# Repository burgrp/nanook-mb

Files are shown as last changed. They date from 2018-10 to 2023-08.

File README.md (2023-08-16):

# NANOOK main control board

Nanook-mb is control board for open source [NANOOK ground-water heat pump](https://cad.onshape.com/documents/2a5990c1c14b1713fdde9141/w/393a2c463278bded31251c68/e/64a137d08251e156e9e96024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) project. The board is responsible for:

- soft-switching three phases compressor
- switching two circulation pumps
- controlling Carel Electronic Expansion Valve
- reading
  - safety low and high pressure switches
  - water temperature sensors on all exchanger ports (eight sensors in total)
  - water pressure sensors on cold and hot side
  - water flow sensors on cold and hot side
  - refrigerant pressure sensors on cold and hot side
- providing configuration web user interface via WiFi connection

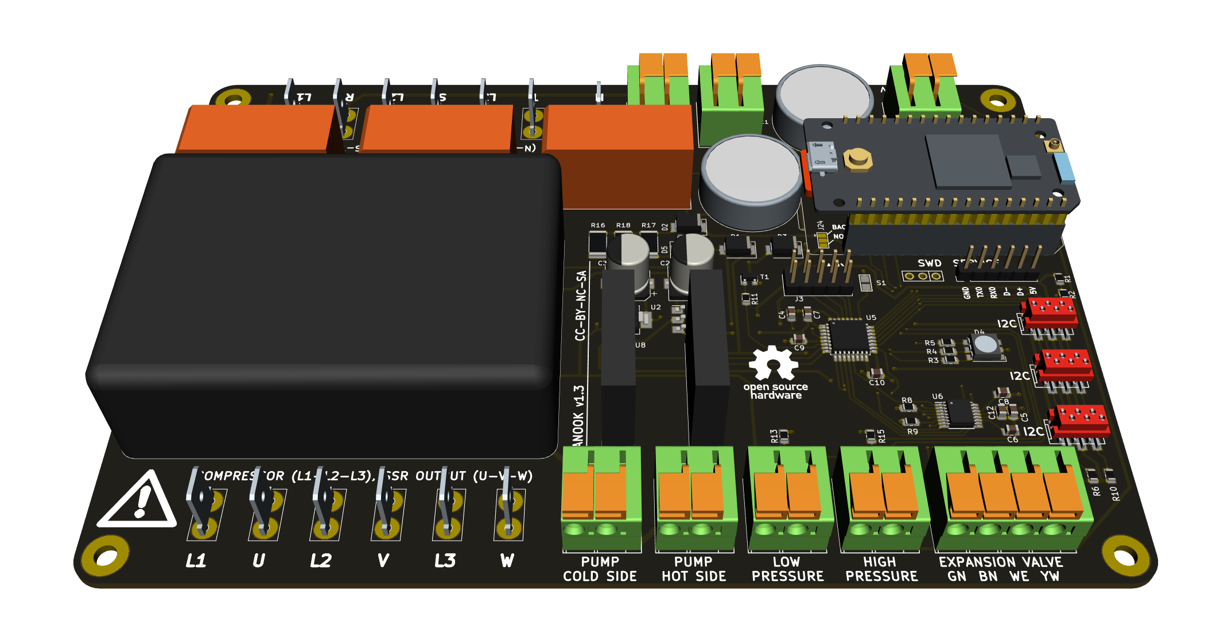
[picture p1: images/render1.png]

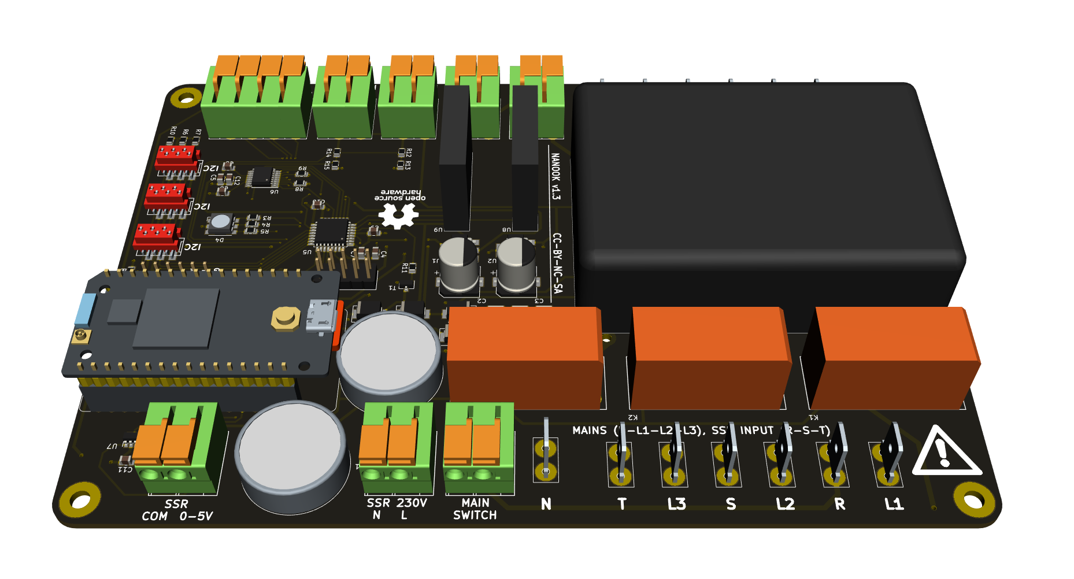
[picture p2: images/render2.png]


## Safety warnings
TBD: grounding, connectors, switching (rocker vs. ext. CB)

## System connections

### Diagram
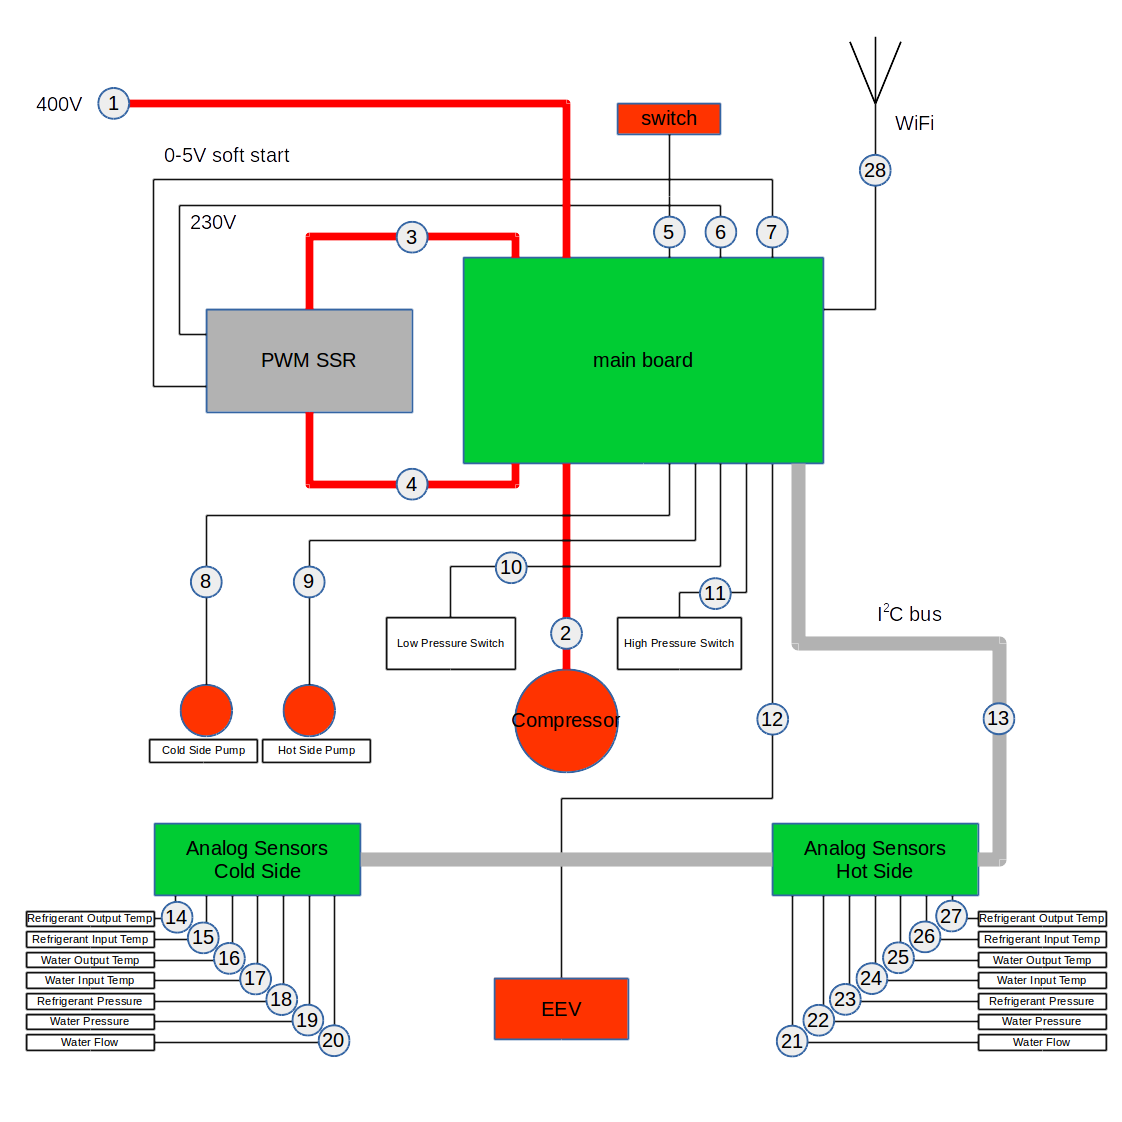
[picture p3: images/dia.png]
Block Diagram


### Wiring

#### Mains to MB (#1)
Connection to mains is done by flexible cable 5x 2.5mm<sup>2</sup>. Mains side should be connected to on-wall box with dedicated circuit breaker (3x16A). Board side end must be terminated with insulated Faston 6.3 connectors and connected to L1, L2, L3 and N terminals of the board. To avoid contact with metal chassis, use angled Fastons only.

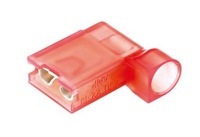
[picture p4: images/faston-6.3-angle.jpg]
Insulated Faston 6.3


Ground wire must be terminated by crimp eye-type connector and mounted by screw to chassis.

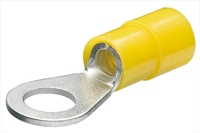
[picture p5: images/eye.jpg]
Eye-type connector


### MB to compressor (#2)
This is, with #1, another high-current connection done by 3x 2.5mm<sup>2</sup> cable. Both sides must be terminated by 6.3 Fastons.

### MB to PWM SSR power lines (#3, #4)
These are six 2.5mm<sup>2</sup> wires terminated by 6.3 Fastons on board side and by eye on SSR side. Make sure all six wires (R, S, T, U, V, W) are connected to properly.

### MB to ON/OFF switch (#5)
There is a rocker switch to turn heat pump ON and OFF. The switch just disconnects onboard power supply, which in turn opens onboard coil relays. This means that the board is still powered even with the rocker switch turned off.

### MB to PWM SSR control lines (#6, #7)
These lines connects main board and PWM SSR control circuit. Two lines supply the control circuit with 230V AC power (#6). The other two are control signal 0-5V. Leave SSR contacts 4-20mA and +5V unconnected.

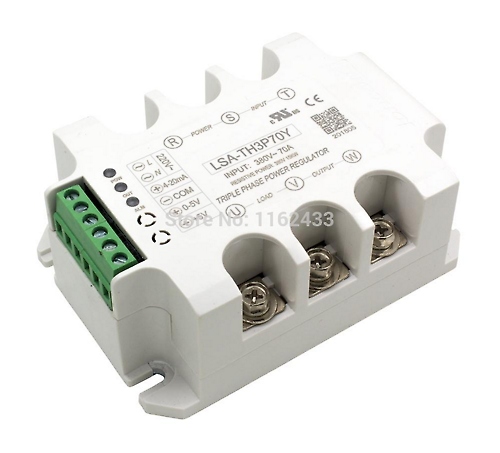
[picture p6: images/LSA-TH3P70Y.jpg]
LSA-TH3P70Y


### MB to circulation pumps (#8, #9)
The main board directly controls primary (cold) and secondary (hot) side circulation pumps. Onboard SSRs are rated to 100W max power output.

### MB to safety pressure switches (#10, #11)
Connections to safety pressure switches on low pressure and high pressure sides.

### MB to electronic expansion valve (#12)
For wires of EEV stepper motor. Color coding for Carel valves is marked on PCB:
- GN - green
- BN - brown
- WE - white
- YW - yellow.

### I<sup>2</sup>C bus (#13)
There are three connectors on board, all of them sharing single I<sup>2</sup>C bus. Analog sensor boards are connected by 6-wire flat cable with crimped Micro-Match connectors.

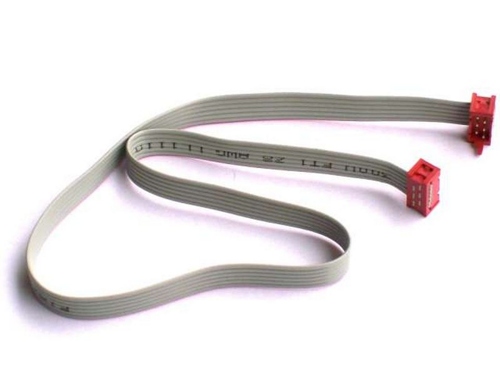
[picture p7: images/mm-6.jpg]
Micro-Match cable


There may be two separate cables for each analog sensors board, or there may be single cable shared by both analog sensors boards.

### Analog sensors board to temperature sensors (#14, #15, #16, #17, #24, #25, #26, #27)
Temperatures are measured by NTC 10K 1% 3950 thermistors.

There are waterproof thermistors with JST-XH connectors available. They may be used directly with no additional crimping needed.

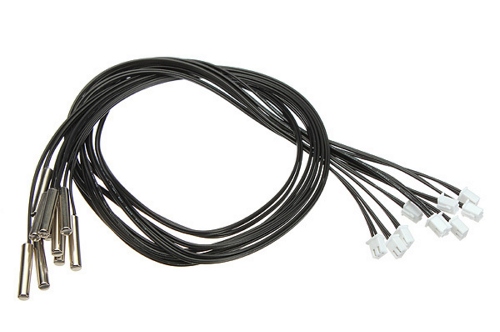
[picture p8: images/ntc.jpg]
Waterproof NTC with JST-XH


Thermistors should be tightly mounted on appropriate pipes, ideally with thermal conductive paste and outer environment insulation cover.

Thermistors are located as follows:
- #14: "cold side refrigerant output" - evaporator refrigerant output to compressor suction
- #15: "cold side refrigerant input" - EEV to evaporator refrigerant input
- #16: "cold side water output" - evaporator water output to collector input
- #17: "cold side water input" - collector output to evaporator water input
- #24: "hot side water input" - cold water from heating system to condenser water input
- #25: "hot side water output" - hot water from condenser to heating system
- #26: "hot side refrigerant input" - compressor discharge to condenser refrigerant input
- #27: "hot side refrigerant output" - condenser refrigerant output to EEV or refrigerant accumulator

### Analog sensors board to pressure sensors (#18, #19, #22, #23)
Pressure sensors are available either with other connectors than JST-XH or with no connector at all. You need to crimp proper three wire JST-XH connectors as:

- 1: GND (black)
- 2: SIGNAL (yellow)
- 3: +5V (red)

and for Carel sensors with green, white and black wires as:

- 1: GND (green)
- 2: SIGNAL (white)
- 3: +5V (black)

Pressure sensors are located as follows:
- #18: "cold side refrigerant pressure" - compressor suction, -1...9,3bar => 0...5V, recommended SPKT0013RO
- #19: "cold side water pressure" - collector water loop, 0...1.2MPa => 0...5V
- #22: "hot side water pressure" - heating system water loop, 0...1.2MPa => 0...5V
- #23: "hot side refrigerant pressure" - compressor discharge, 0...34,5bar => 0...5V, recommended SPKT0033RO

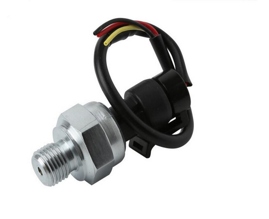
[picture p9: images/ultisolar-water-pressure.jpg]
Ultisolar water pressure sensor 0...1.2MPa


Ultisolar water pressure sensor 0...1.2MPa

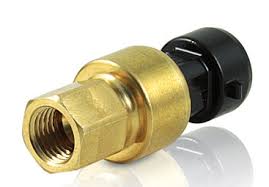
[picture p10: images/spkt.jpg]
Carel SPKT refrigerant pressure sensor


Carel SPKT refrigerant pressure sensor

### Analog sensors board to water flow sensors (#20, #21)
Water flow sensors are available either with other connectors than JST-XH or with no connector at all. You need to crimp proper three wire JST-XH connectors as
- 1: GND (black)
- 2: SIGNAL (yellow)
- 3: +5V (red)

Water sensors are located as follows:
- #20: "cold side water flow" - collector water loop
- #21: "hot side water flow" - heating system water loop

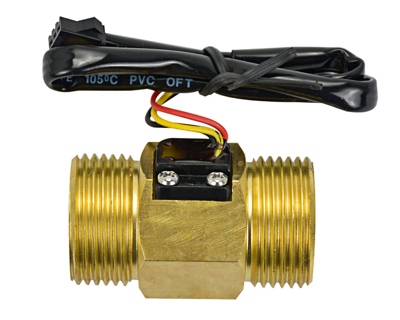
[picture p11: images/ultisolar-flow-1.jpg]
Ultisolar flow sensor


USC-HS10TA BSP is a suitable water flow sensor

### MB to WiFi antenna (#28)

Main board is connected to network by WiFi. Although there is small chip antenna integrated on board, an external antenna is needed because of metal enclosure. Connect a 2.4GHz antenna by IPEX connector.

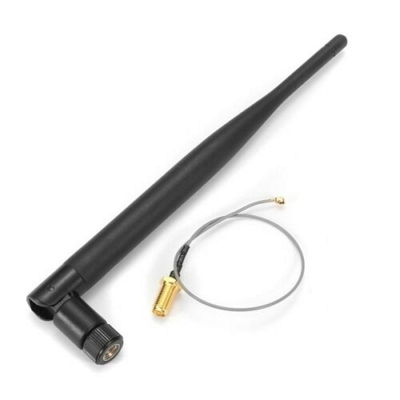
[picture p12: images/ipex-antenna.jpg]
IPEX 2.4GHz panel mount antenna


## Compiling firmware
In order to compile and flash firmware, you need to install Node.js, openocd and arm-none-eabi GCC.

Source code is written our [Silicon build system](https://github.com/device-farm/silicon).
Install Silicon by:
```sh
sudo npm install -g @device.farm/silicon
```

And then build and flash by:
```sh
silicon build -dsf
```

The `-f` parameter instructs Silicon to flash the image using openocd, which should be connected to your MCU and listening on port 4444.

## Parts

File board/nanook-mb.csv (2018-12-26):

Quantity | Designator | Designation
2 | C13,C1 | 2F
4 | REF**,REF**,REF**,REF** | MountingHole_3.7mm_Pad
3 | K3,K1,K2 | RELAY_2
6 | C4,C7,C9,C10,C11,C12 | 100n
1 | C5 | 10u
1 | C6 | 10n
1 | C8 | 2.2M
4 | D1,D3,D2,D5 | SK22
1 | J1 | Power Switch
1 | J3 | AUX
1 | J4 | E2V
1 | J5 | LPS
1 | J6 | Pump Cold Side
1 | J7 | Pump Hot Side
1 | J8 | HPS
9 | R1,R2,R6,R7,R10,R12,R13,R14,R15 | 4k7
3 | R3,R4,R5 | 270R
2 | R8,R9 | 0R22
1 | R11 | 1K5
1 | S1 | SB2P
1 | T1 | BC817
2 | U1,U2 | NCP1117-3.3_SOT223
1 | U3 | Mean Well PM-15-5
1 | U5 | STM32F030K6Tx
1 | U7 | MCP4706A0T-E/CH
2 | U8,U9 | G3MB-5V-SSR
1 | X1 | SWD
1 | X2 | I2C Cold Side
1 | X3 | I2C Hot Side
1 | X4 | I2C Aux
1 | D4 | LED_RGB
3 | R16,R17,R18 | 4R7/2W
1 | J10 | Service
1 | U6 | DRV8833
1 | J13 | SSR 220
1 | J14 | SSR 0-5V
1 | J15 | Compressor L1
1 | J16 | Compressor L2
1 | J17 | Compressor L3
1 | J18 | SSR Output L1
1 | J19 | SSR Output L2
1 | J20 | SSR Output L3
1 | J21 | SSR Input L1
1 | J22 | SSR Input L2
1 | J23 | SSR Input L3
1 | J2 | Mains L1
1 | J9 | Mains L2
1 | J11 | Mains L3
1 | J12 | Mains N
1 | REF*** | OSHW-Logo_11.4x12mm_SilkScreen
2 | C2,C3 | 1m
1 | J24 | GS3
1 | M1 | NanoPi-Duo

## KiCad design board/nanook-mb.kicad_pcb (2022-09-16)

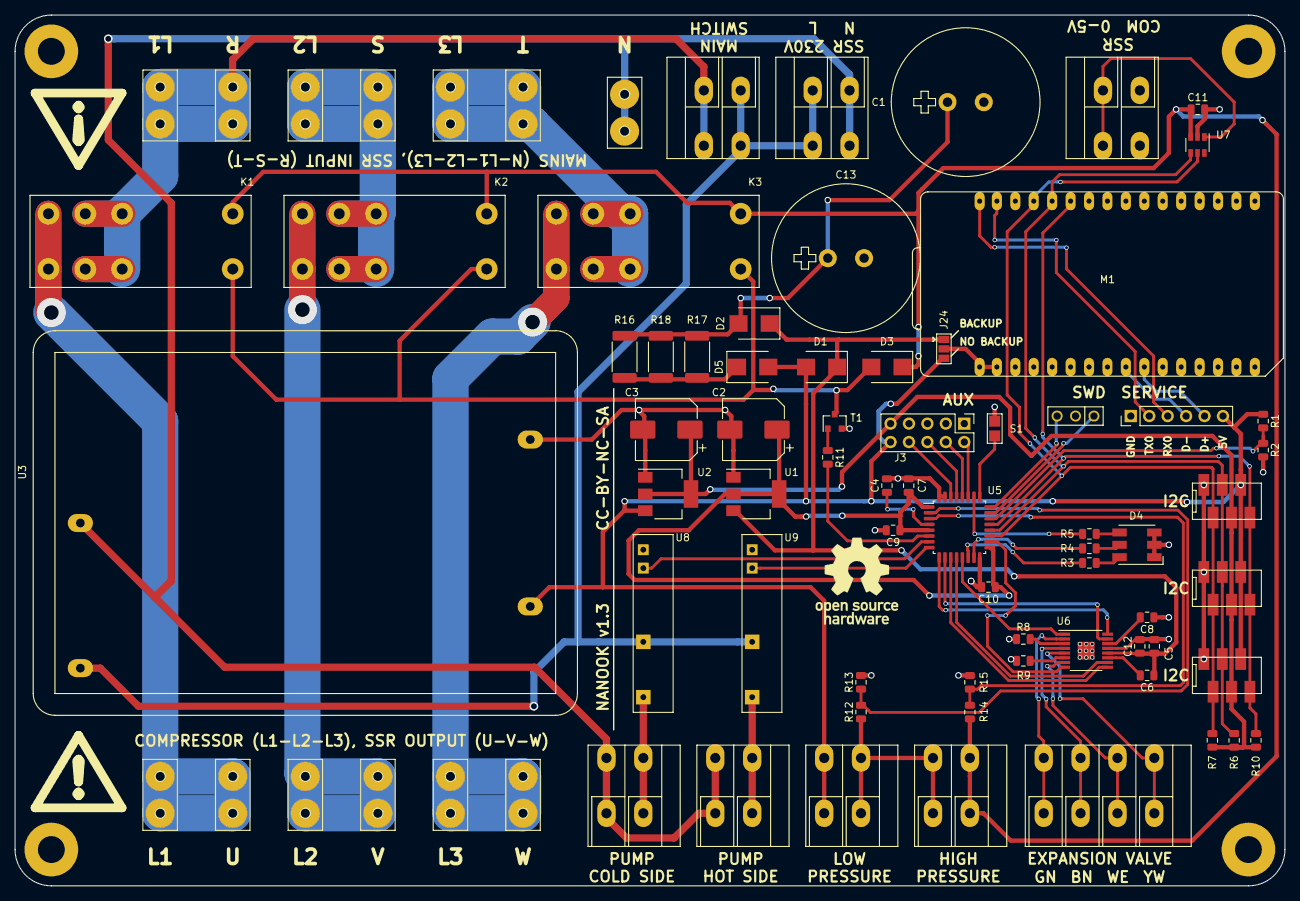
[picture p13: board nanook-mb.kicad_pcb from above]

Board: 2 copper layers, 175.0 x 120.0 mm, 78 parts (0 on the bottom side), 64 nets.

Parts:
C1, C13: 2F; BCE005R5C205FS
C2, C3: 1m; CP_Elec_8x10
C4, C7, C9, C10, C11, C12: 100n; C_0805_2012Metric
C5: 10u; C_0805_2012Metric
C6: 10n; C_0805_2012Metric
C8: 2.2M; C_0805_2012Metric
D1, D2, D3, D5: SK22; D_SMB
D4: LED_RGB; LED_RGB_5050-6
J1: Power Switch; DG142R-2-5.08
J2: Mains L1; Tab-6.3
J3: AUX; PinHeader_2x05_P2.54mm_Vertical
J4: E2V; DG142R-4-5.08
J5: LPS; DG142R-2-5.08
J6: Pump Cold Side; DG142R-2-5.08
J7: Pump Hot Side; DG142R-2-5.08
J8: HPS; DG142R-2-5.08
J9: Mains L2; Tab-6.3
J10: Service; PinHeader_1x06_P2.54mm_Vertical
J11: Mains L3; Tab-6.3
J12: Mains N; Tab-6.3
J13: SSR 220; DG142R-2-5.08
J14: SSR 0-5V; DG142R-2-5.08
J15: Compressor L1; Tab-6.3
J16: Compressor L2; Tab-6.3
J17: Compressor L3; Tab-6.3
J18: SSR Output L1; Tab-6.3
J19: SSR Output L2; Tab-6.3
J20: SSR Output L3; Tab-6.3
J21: SSR Input L1; Tab-6.3
J22: SSR Input L2; Tab-6.3
J23: SSR Input L3; Tab-6.3
J24: GS3; SolderJumper-3_P1.3mm_Open_Pad1.0x1.5mm
K1, K2, K3: RELAY_2; RT314_Relay
M1: NanoPi-Duo
R1, R2, R6, R7, R10, R12, R13, R14, R15: 4k7; R_0805_2012Metric
R3, R4, R5: 270R; R_0805_2012Metric
R8, R9: 0R22; R_0805_2012Metric
R11: 1K5; R_0805_2012Metric
R16, R17, R18: 4R7/2W; R_2512_6332Metric
S1: SB2P
T1: BC817; SOT-23
U1, U2: NCP1117-3.3_SOT223; SOT-223-3_TabPin2
U3: Mean Well PM-15-5; Mean-Well-PM-15-5
U5: STM32F030K6Tx; LQFP-32_7x7mm_P0.8mm
U6: DRV8833; TSSOP-16_4.4x5mm_Pitch0.65mm-EP
U7: MCP4706A0T-E/CH; SOT-23-6
U8, U9: G3MB-5V-SSR; G3MB-SSR
X1: SWD
X2: I2C Cold Side; Micro-Match-FOB-6
X3: I2C Hot Side; Micro-Match-FOB-6
X4: I2C Aux; Micro-Match-FOB-6

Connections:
+3V3: C3.1, J3.9, R6.1, R7.1, R10.1, U2.2, X2.4, X3.4, X4.4
+5V: D1.2, D5.2, J3.10, J5.1, J10.6, J24.3, R1.1, U2.3, U3.4, X2.5, X3.5, X4.5
/3V3_BACKUP: C2.1, C7.1, C9.1, C10.1, U1.2, U5.1, U5.5, U5.17
/5V_BACKUP: C5.2, C6.1, C12.1, D1.1, D2.1, J24.1, U1.3, U6.12
/ALERT: M1.22, R10.2, U5.21, X2.6, X3.6, X4.6
/BACKUP_C: C1.1, C13.1, D2.2, R16.1, R17.1, R18.1
/COMP_5V: C11.1, D3.1, J8.2, K1.A1, K2.A1, K3.A1, R14.1, U7.3
/COMP_L1: J15.1, J18.1, K1.14, K1.24
/COMP_L2: J16.1, J19.1, K2.14, K2.24
/COMP_L3: J17.1, J20.1, K3.14, K3.24
/COMP_RAMP: J14.2, U7.1
/COMP_RELAY: R11.2, U5.6
/COMP_RELAY_PWR: D3.2, K1.A2, K2.A2, K3.A2, T1.3
/E2V_A1: U5.9, U6.16
/E2V_A2: U5.10, U6.15
/E2V_B1: U5.11, U6.9
/E2V_B2: U5.12, U6.10
/E2V_NFAULT: U5.18, U6.8
/E2V_NSLEEP: U5.13, U6.1
/HPS: R14.2, R15.1, U5.3
/LPS: R12.2, R13.1, U5.2
/MAINS_L1: J1.2, J2.1, J21.1, K1.11, K1.12, K1.21, K1.22
/MAINS_L2: J9.1, J22.1, K2.11, K2.12, K2.21, K2.22
/MAINS_L3: J11.1, J23.1, K3.11, K3.12, K3.21, K3.22
/MAINS_N: J6.1, J7.1, J12.1, J13.1, U3.2
/PUMP_COLD_SIDE: U5.7, U8.3
/PUMP_HOT_SIDE: U5.8, U9.3
/PWR_OK: R1.2, R2.1, U5.22
/RX0: J10.3, M1.17
/SCL: M1.20, R7.2, U5.19, U7.5, X2.2, X3.2, X4.2
/SDA: M1.21, R6.2, U5.20, U7.4, X2.3, X3.3, X4.3
/SWCLK: U5.24, X1.3
/SWDIO: U5.23, X1.1
/SWITCHED_L: J1.1, J13.2, U3.1, U8.2, U9.2
/TX0: J10.2, M1.18
/USB-DM: J10.4, M1.8
/USB-DP: J10.5, M1.7
GND: C1.2, C2.2, C3.2, C4.2, C5.1, C7.2, C8.1, C9.2, C10.2, C11.2, C12.2, C13.2, D4.1, D4.2, D4.3, J3.1, J3.3, J3.5, J3.7, J10.1, J14.1, M1.13, M1.19, R2.2, R8.1, R9.1, R13.2, R15.2, S1.2, T1.2, U1.1, U2.1, U3.3, U5.16, U5.31, U5.32, U6.13, U6.17, U7.2, U8.4, U9.4, X1.2, X2.1, X3.1, X4.1
unnamed: C4.1, U5.4
unnamed: C6.2, U6.11
unnamed: C8.2, U6.14
unnamed: D4.4, R5.2
unnamed: D4.5, R4.2
unnamed: D4.6, R3.2
unnamed: D5.1, R16.2, R17.2, R18.2
unnamed: J3.2, U5.27
unnamed: J3.4, U5.28
unnamed: J3.6, U5.29
unnamed: J3.8, U5.30
unnamed: J4.1, U6.2
unnamed: J4.2, U6.4
unnamed: J4.3, U6.7
unnamed: J4.4, U6.5
unnamed: J5.2, J8.1, R12.1
unnamed: J6.2, U8.1
unnamed: J7.2, U9.1
unnamed: J24.2, M1.15, M1.16
unnamed: R3.1, U5.14
unnamed: R4.1, U5.15
unnamed: R5.1, U5.26
unnamed: R8.2, U6.3
unnamed: R9.2, U6.6
unnamed: R11.1, T1.1
unnamed: S1.1, U5.25

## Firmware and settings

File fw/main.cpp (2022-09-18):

const int VALUE_UNKNOWN = -1;

enum Command {
  CMD_NONE,
  CMD_I2C_SET_RGB_LED,
  CMD_RUN_EEV,
  CMD_SET_OUTPUT,
  CMD_SET_EEV
};

const int outputPinsCount = 3;
const int inputPinsCount = 5;

const int pwrOkPin = 12;

class GWHP : public i2c::hw::BufferedSlave {

  struct __attribute__((packed)) {
    unsigned char command;
    union {
      rgbLed::Setting rgbLed;
      struct __attribute__((packed)) {
        short fullSteps;
        unsigned char fast;
      } runEev;
      struct __attribute__((packed)) {
        unsigned char outputIndex;
        unsigned char state;
      } setOutput;
      struct __attribute__((packed)) {
        int position;
      } setEev;
    };
  } i2cRxBuffer;

  struct __attribute__((packed)) {
    unsigned char outputs;
    unsigned char inputs;
    int eevPosition;
  } i2cTxBuffer;

  struct {
    rgbLed::Setting test = {.rampUpTime = 0,
                            .onTime = 255,
                            .rampDownTime = 0,
                            .offTime = 0,
                            .rgb = {255, 255, 255}};
    rgbLed::Setting ready = {.rampUpTime = 150,
                             .onTime = 0,
                             .rampDownTime = 5,
                             .offTime = 10,
                             .rgb = {220, 255, 0}};
  } rgbSettings;

public:
  iwdg::Driver iwdg;

  rgbLed::Driver rgbLed;
  eev::Driver eev;

  outputPin::Driver outputPins[outputPinsCount];
  inputPin::Driver inputPins[inputPinsCount];

  void init(int i2cAddress) {

    iwdg.init();

    outputPins[0].init(&target::GPIOA, 0, 0); // compressor relay
    outputPins[1].init(&target::GPIOA, 1, 0); // pump cold side
    outputPins[2].init(&target::GPIOA, 2, 0); // pump hot side

    inputPins[0].init(&target::GPIOA, 8, true, false);  // EEV NFAULT
    inputPins[1].init(&target::GPIOA, 11, true, false); // I2C ALERT
    inputPins[2].init(&target::GPIOA, pwrOkPin, false, true);
    inputPins[3].init((volatile target::gpio_a::Peripheral *)&target::GPIOF, 0,
                      false, true); // LPS
    inputPins[4].init((volatile target::gpio_a::Peripheral *)&target::GPIOF, 1,
                      false, true); // HPS

    // EEV
    eev.init(&target::GPIOA, 3, 4, 5, 6, 7, &target::TIM17);

    // RGB LED
    rgbLed.init(&target::GPIOB, 3, 1, 0, &target::TIM16, &rgbSettings.test);

    for (volatile int c = 0; c < 100000; c++)
      ;

    rgbLed.set(&rgbSettings.ready);

    // I2C
    target::GPIOA.AFRH.setAFRH(9, 4);
    target::GPIOA.AFRH.setAFRH(10, 4);
    target::GPIOA.MODER.setMODER(9, 2);
    target::GPIOA.MODER.setMODER(10, 2);
    BufferedSlave::init(&target::I2C1, i2cAddress,
                        (unsigned char *)&i2cRxBuffer, sizeof(i2cRxBuffer),
                        (unsigned char *)&i2cTxBuffer, sizeof(i2cTxBuffer));

    eev.run(500, true);
  }

  virtual void onTxStart() {
    i2cTxBuffer.outputs = 0;
    for (int c = 0; c < outputPinsCount; c++) {
      i2cTxBuffer.outputs |= outputPins[c].get() << c;
    }
    i2cTxBuffer.inputs = 0;
    for (int c = 0; c < inputPinsCount; c++) {
      i2cTxBuffer.inputs |= inputPins[c].get() << c;
    }
    i2cTxBuffer.eevPosition = eev.getPosition();
  }

  virtual void onStop(bool read) {
    if (!read) {
      Command command = (Command)i2cRxBuffer.command;
      i2cRxBuffer.command = CMD_NONE;
      switch (command) {
      case CMD_I2C_SET_RGB_LED: {
        rgbLed.set(&i2cRxBuffer.rgbLed);
        break;
      }
      case CMD_RUN_EEV: {
        eev.run(i2cRxBuffer.runEev.fullSteps, i2cRxBuffer.runEev.fast);
        break;
      }
      case CMD_SET_OUTPUT: {
        if (i2cRxBuffer.setOutput.outputIndex < outputPinsCount) {
          outputPins[i2cRxBuffer.setOutput.outputIndex].set(
              i2cRxBuffer.setOutput.state);
        }
        break;
      }
      case CMD_SET_EEV: {
        eev.setPosition(i2cRxBuffer.setEev.position);
        break;
      }
      }
    }
  }

  void handlePwrOkInterrupt() {
    if (target::EXTI.PR.getPR(pwrOkPin)) {
      // reboot on both edges, no need to clear interrupt
      iwdg.reboot();
    }
  }
};

GWHP gwhp;

void interruptHandlerI2C1() { gwhp.handleInterrupt(); }

void interruptHandlerTIM16() { gwhp.rgbLed.handleInterrupt(); }

void interruptHandlerTIM17() { gwhp.eev.handleInterrupt(); }

void interruptHandlerEXTI4_15() { gwhp.handlePwrOkInterrupt(); }

void initApplication() {

  target::RCC.AHBENR.setIOPAEN(true);
  target::RCC.AHBENR.setIOPBEN(true);
  target::RCC.AHBENR.setIOPFEN(true);
  target::RCC.APB1ENR.setC_EN(1, 1);
  target::RCC.APB2ENR.setTIM16EN(1);
  target::RCC.APB2ENR.setTIM17EN(1);

  target::NVIC.ISER.setSETENA(1 << target::interrupts::External::I2C1);
  target::NVIC.ISER.setSETENA(1 << target::interrupts::External::TIM16);
  target::NVIC.ISER.setSETENA(1 << target::interrupts::External::TIM17);
  target::NVIC.ISER.setSETENA(1 << target::interrupts::External::EXTI4_15);

  target::SYSCFG.EXTICR4.setEXTI(pwrOkPin, 0);
  target::EXTI.IMR.setMR(pwrOkPin, 1);
  target::EXTI.FTSR.setTR(pwrOkPin, 1);
  target::EXTI.RTSR.setTR(pwrOkPin, 1);

  gwhp.init(0x74);
}

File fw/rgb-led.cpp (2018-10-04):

namespace rgbLed {

struct __attribute__ ((packed)) Setting {
    unsigned char rampUpTime;
    unsigned char onTime;
    unsigned char rampDownTime;
    unsigned char offTime;
    unsigned char rgb[3];
};

class Driver {

    volatile target::gpio_b_f::Peripheral* port;
    int pins[3];
    int pwmCnt;
    int pwm[3];
    int stepPrescaler;
    int stepTimer;
    int stepEnd = 0xFF;
    int step;

    Setting setting;

    volatile target::tim_16_17::Peripheral* timer;

public:
    void init(
        volatile target::gpio_b_f::Peripheral* port,
        int pinR,
        int pinG,
        int pinB,
        volatile target::tim_16_17::Peripheral* timer,
        Setting* setting
    ) {
        this->port = port;
        this->pins[0] = pinR;
        this->pins[1] = pinG;
        this->pins[2] = pinB;
        this->timer = timer;
        this->setting = *setting;

        for (int c = 0; c < sizeof(pins); c++) {
            port->MODER.setMODER(pins[c], 1);
        }

        timer->DIER.setUIE(1);
        timer->ARR.setARR(0x200);

        timer->CR1.setCEN(1);

        stepStart();
        update();
    }

    void update() {
        if (setting.rampUpTime == 0 && setting.onTime == 0 & setting.rampDownTime == 0 && setting.offTime == 0) {
            for (int c = 0; c < 3; c++) {
                pwm[c] = setting.rgb[c];
            }
        } else {
            int intensity = 0;        
            if (step == 0) {
                intensity = 0xFF * stepTimer / stepEnd;
            } else if (step == 1) {
                intensity = 0xFF;
            } else if (step == 2) {
                intensity = 0xFF - (0xFF * stepTimer / stepEnd);
            } 
            for (int c = 0; c < 3; c++) {
                pwm[c] = (setting.rgb[c] * (intensity + 1)) >> 8;
            }
        }
    }

    void stepStart() {
        if (step == 0) {
            stepEnd = setting.rampUpTime;
        } else if (step == 1) {
            stepEnd = setting.onTime;
        } else if (step == 2) {
            stepEnd = setting.rampDownTime;
        } else if (step == 3) {
            stepEnd = setting.offTime;
        } 
        if (stepEnd == 0) {
            stepEnd = 1;
        }
    }

    void handleInterrupt() {
        timer->SR.setUIF(0);
        pwmCnt = (pwmCnt + 1) & 0xFF;
        for (int c = 0; c < 3; c++) {
            port->ODR.setODR(pins[c], pwmCnt < pwm[c] || pwm[c] == 0xFF);
        } 
        stepPrescaler++;
        if (stepPrescaler == 250) {
            stepPrescaler = 0;
            stepTimer++;
            if (stepTimer == stepEnd) {
                stepTimer = 0;                
                step++;
                if (step == 5) {
                    step = 0;
                }
                stepStart();
            }
            update();
        }
    }

    void set(Setting* setting) {
        this->setting = *setting;
        update();
    }
};

}

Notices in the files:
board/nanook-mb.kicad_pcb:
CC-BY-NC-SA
